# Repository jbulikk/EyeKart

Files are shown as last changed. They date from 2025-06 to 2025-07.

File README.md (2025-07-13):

# EyeKart

A gimbal system that mimics the user's head movements in real time.
The project is divided into two cooperating parts: a transmitting unit and a receiving unit.

- The transmitting module uses an IMU sensor to capture the user's head orientation.

- The motion data is processed and wirelessly transmitted to the receiving module.

- The receiving module interprets the incoming data and controls servo motors to adjust the mechanical gimbal accordingly, replicating the user's head movement.

imu_diagram
gimbal_diagram

# Overview

🎥 [Demo 1](https://youtu.be/xsn1YAiG0OE)  
🎥 [Demo 2](https://youtu.be/Qv6_rfJNsOU)

<br/>

IMG_E6707
IMG_E6706

<br/>

IMG_E6712

<br/>

IMG_E6708
IMG_E6710

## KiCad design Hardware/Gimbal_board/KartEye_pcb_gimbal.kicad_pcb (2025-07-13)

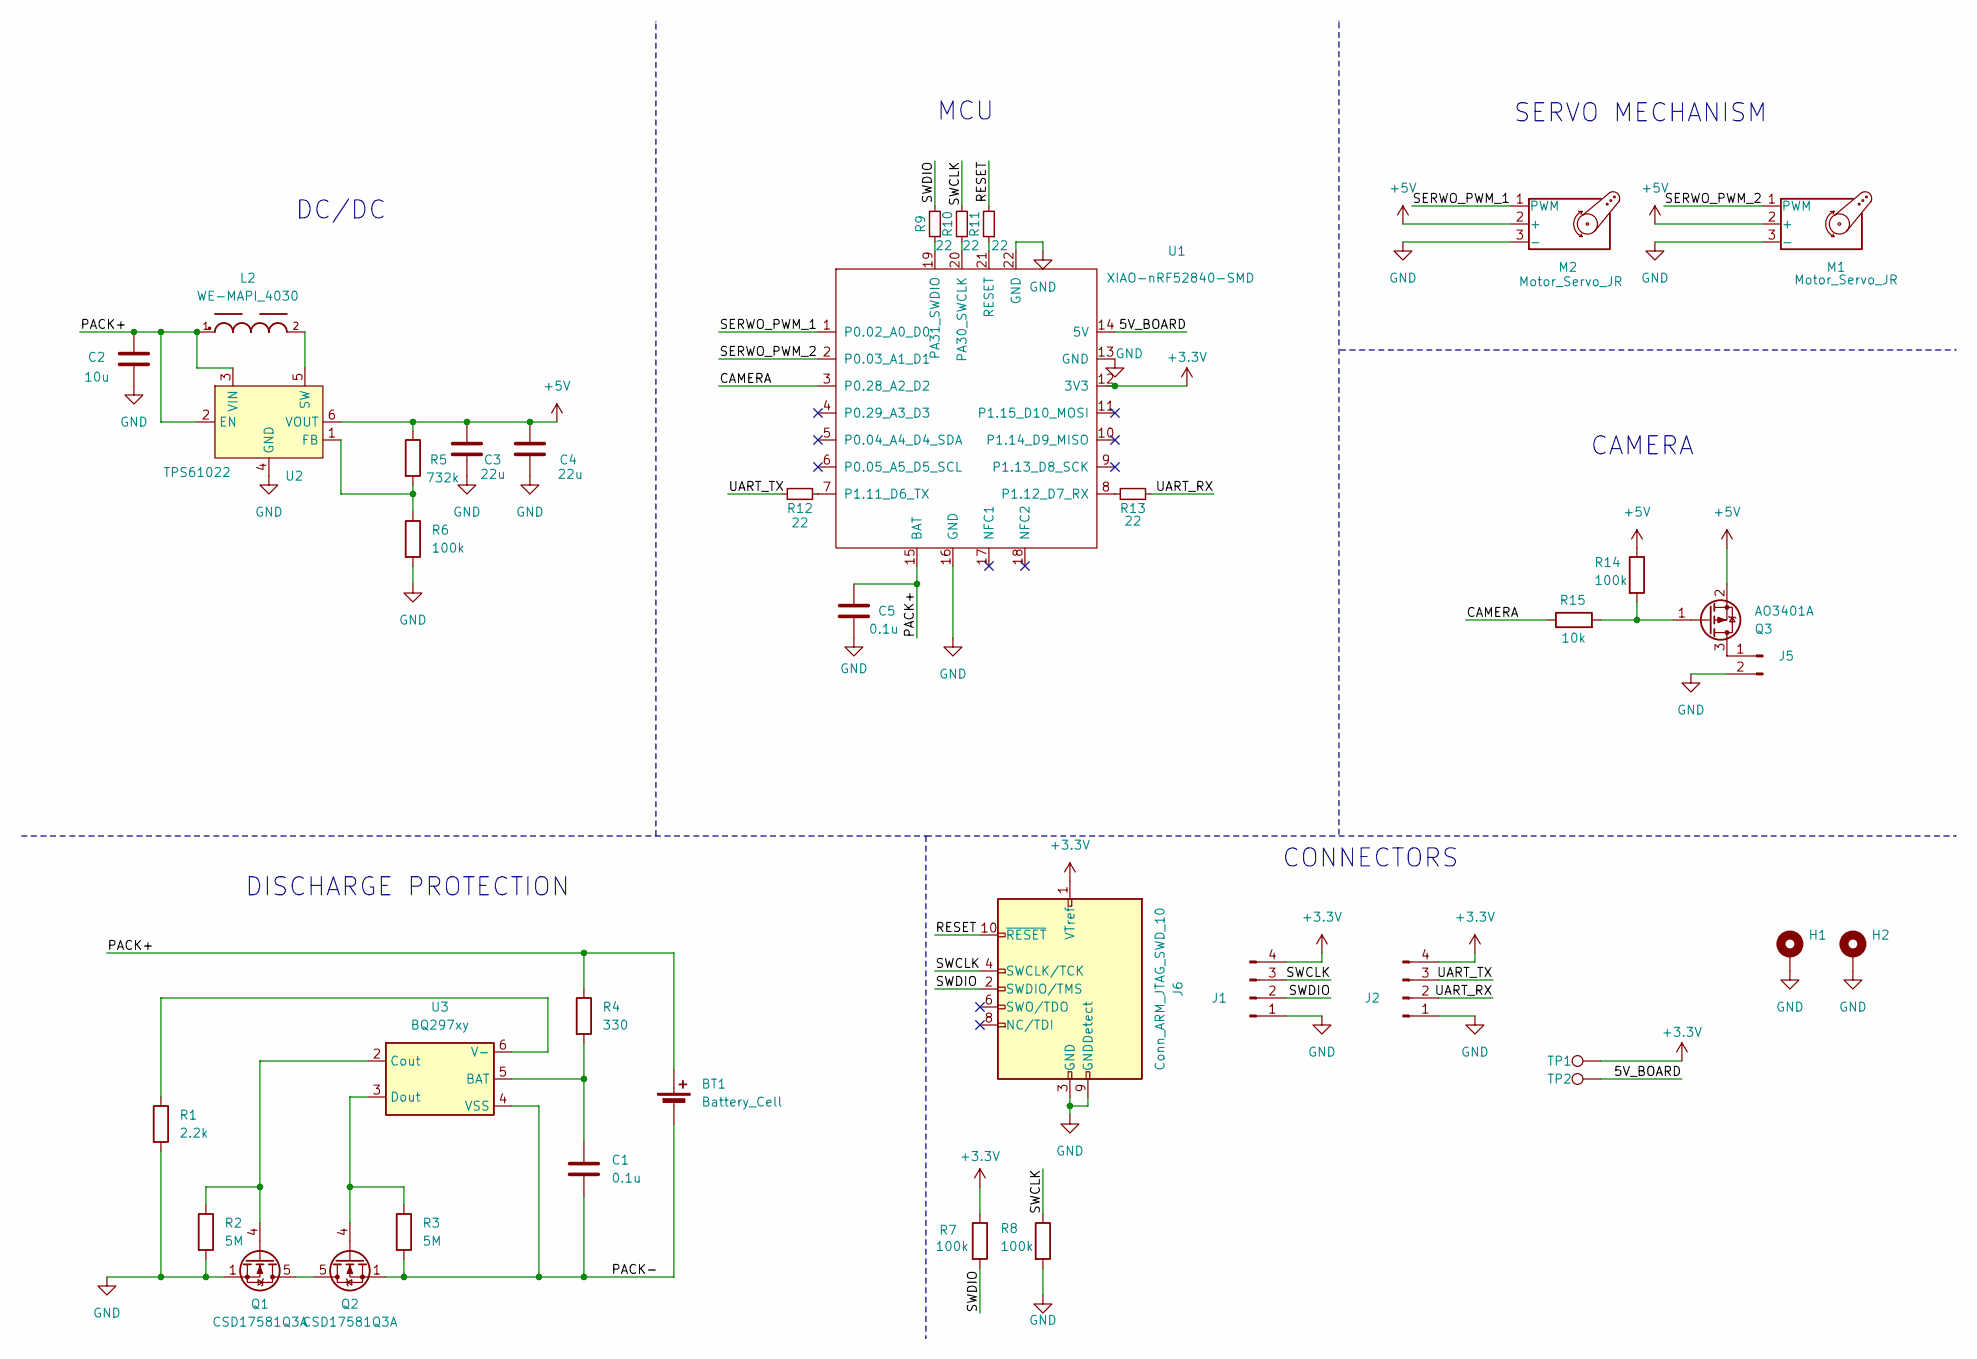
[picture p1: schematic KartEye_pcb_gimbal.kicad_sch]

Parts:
BT1: Battery_Cell; JST_XH_B2B-XH-A_1x02_P2.50mm_Vertical
C1, C5: 0.1u; C_0805_2012Metric_Pad1.18x1.45mm_HandSolder
C2: 10u; C_0805_2012Metric_Pad1.18x1.45mm_HandSolder
C3, C4: 22u; C_0805_2012Metric_Pad1.18x1.45mm_HandSolder
H1, H2: MountingHole_Pad; MountingHole_2.2mm_M2_DIN965_Pad
J1, J2: Conn_01x04_Pin; PinHeader_1x04_P2.54mm_Vertical
J5: Conn_01x02_Pin; Molex_PicoBlade_53047-0210_1x02_P1.25mm_Vertical
J6: Conn_ARM_JTAG_SWD_10; PinHeader_2x05_P1.27mm_Vertical_SMD
L2: WE-MAPI_4030
M1, M2: Motor_Servo_JR; PinHeader_1x03_P2.54mm_Vertical
Q1, Q2: CSD17581Q3A; VSON-8_3.3x3.3mm_P0.65mm_NexFET
Q3: AO3401A; SOT-23
R1: 2.2k; R_0805_2012Metric_Pad1.20x1.40mm_HandSolder
R2, R3: 5M; R_0805_2012Metric_Pad1.20x1.40mm_HandSolder
R4: 330; R_0805_2012Metric_Pad1.20x1.40mm_HandSolder
R5: 732k; R_0805_2012Metric_Pad1.20x1.40mm_HandSolder
R6, R7, R8, R14: 100k; R_0805_2012Metric_Pad1.20x1.40mm_HandSolder
R9, R10, R11, R12, R13: 22; R_0805_2012Metric_Pad1.20x1.40mm_HandSolder
R15: 10k; R_0805_2012Metric_Pad1.20x1.40mm_HandSolder
TP1, TP2: TestPoint; TestPoint_Pad_1.0x1.0mm
U1: XIAO-nRF52840-SMD
U2: TPS61022; SOT-563
U3: BQ297xy; WSON-6_1.5x1.5mm_P0.5mm

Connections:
+3.3V: J1.4, J2.4, J6.1 (VTref), R7.1, TP1.1, U1.12 (3V3)
+5V: C3.1, C4.1, M1.2 (+), M2.2 (+), Q3.2 (S), R5.1, R14.1, U2.6 (VOUT)
/5V_BOARD: TP2.1, U1.14 (5V)
/CAMERA: R15.1, U1.3 (P0.28_A2_D2)
/PACK+: BT1.1 (+), C2.1, C5.1, L2.1, R4.1, U1.15 (BAT), U2.2 (EN), U2.3 (VIN)
/PACK-: BT1.2 (-), C1.2, Q2.1 (S), Q2.2 (S), Q2.3 (S), R3.2, U3.4 (VSS)
/RESET: J6.10 (~RESET), R11.2
/SERWO_PWM_1: M2.1 (PWM), U1.1 (P0.02_A0_D0)
/SERWO_PWM_2: M1.1 (PWM), U1.2 (P0.03_A1_D1)
/SWCLK: J1.3, J6.4 (SWCLK/TCK), R8.1, R10.2
/SWDIO: J1.2, J6.2 (SWDIO/TMS), R7.2, R9.2
/UART_RX: J2.2, R13.1
/UART_TX: J2.3, R12.2
GND: C2.2, C3.2, C4.2, C5.2, H1.1, H2.1, J1.1, J2.1, J5.2, J6.3 (GND), J6.5 (GND), J6.9 (GNDDetect), M1.3 (-), M2.3 (-), Q1.1 (S), Q1.2 (S), Q1.3 (S), R1.2, R2.2, R6.2, R8.2, U1.13 (GND), U1.16 (GND), U1.22 (GND), U2.4 (GND)
unnamed: J5.1, Q3.3 (D)
unnamed: Q1.5 (D), Q2.5 (D)
unnamed: Q1.4 (G), R2.1, U3.2 (Cout)
unnamed: Q2.4 (G), R3.1, U3.3 (Dout)
unnamed: Q3.1 (G), R14.2, R15.2
unnamed: R12.1, U1.7 (P1.11_D6_TX)
unnamed: R13.2, U1.8 (P1.12_D7_RX)
unnamed: R10.1, U1.20 (PA30_SWCLK)
unnamed: R9.1, U1.19 (PA31_SWDIO)
unnamed: R11.1, U1.21 (RESET)
unnamed: R5.2, R6.1, U2.1 (FB)
unnamed: L2.2, U2.5 (SW)
unnamed: C1.1, R4.2, U3.5 (BAT)
unnamed: R1.1, U3.6 (V-)

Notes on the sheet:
CONNECTORS
SERVO MECHANISM
DC/DC
MCU
DISCHARGE PROTECTION
CAMERA

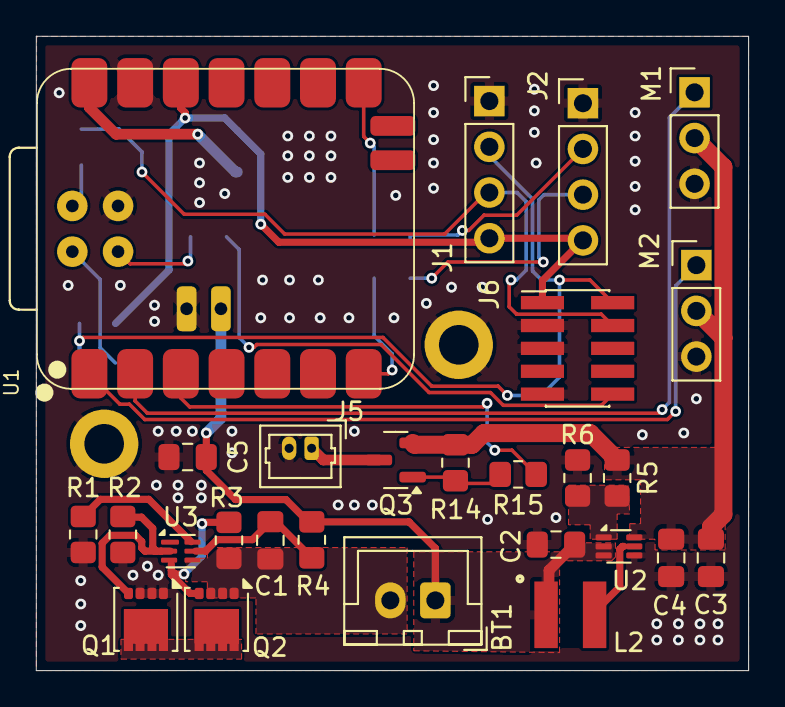
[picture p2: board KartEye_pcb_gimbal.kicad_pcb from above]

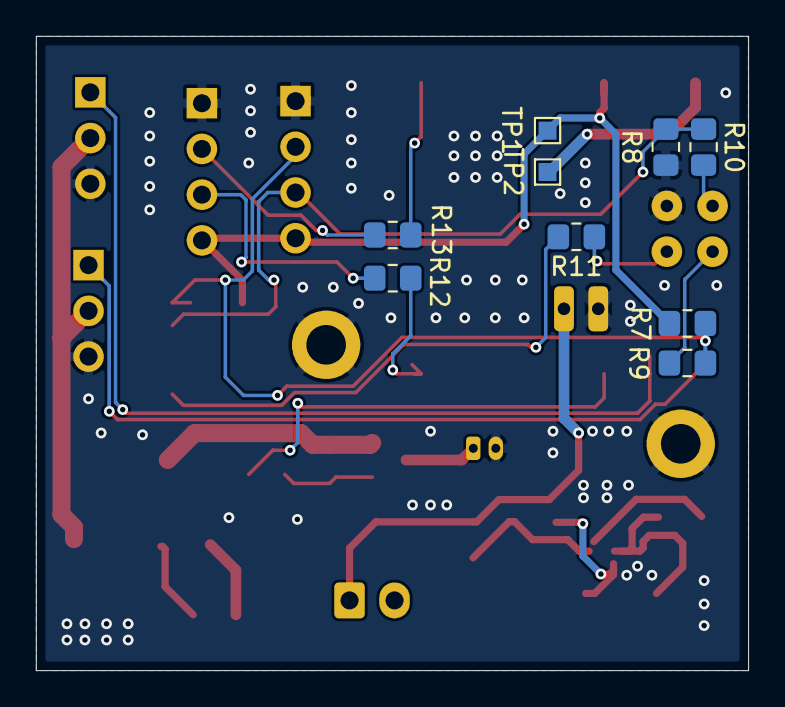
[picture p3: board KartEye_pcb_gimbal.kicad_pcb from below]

Board: 2 copper layers, 39.6 x 35.2 mm, 38 parts (9 on the bottom side), 28 nets.

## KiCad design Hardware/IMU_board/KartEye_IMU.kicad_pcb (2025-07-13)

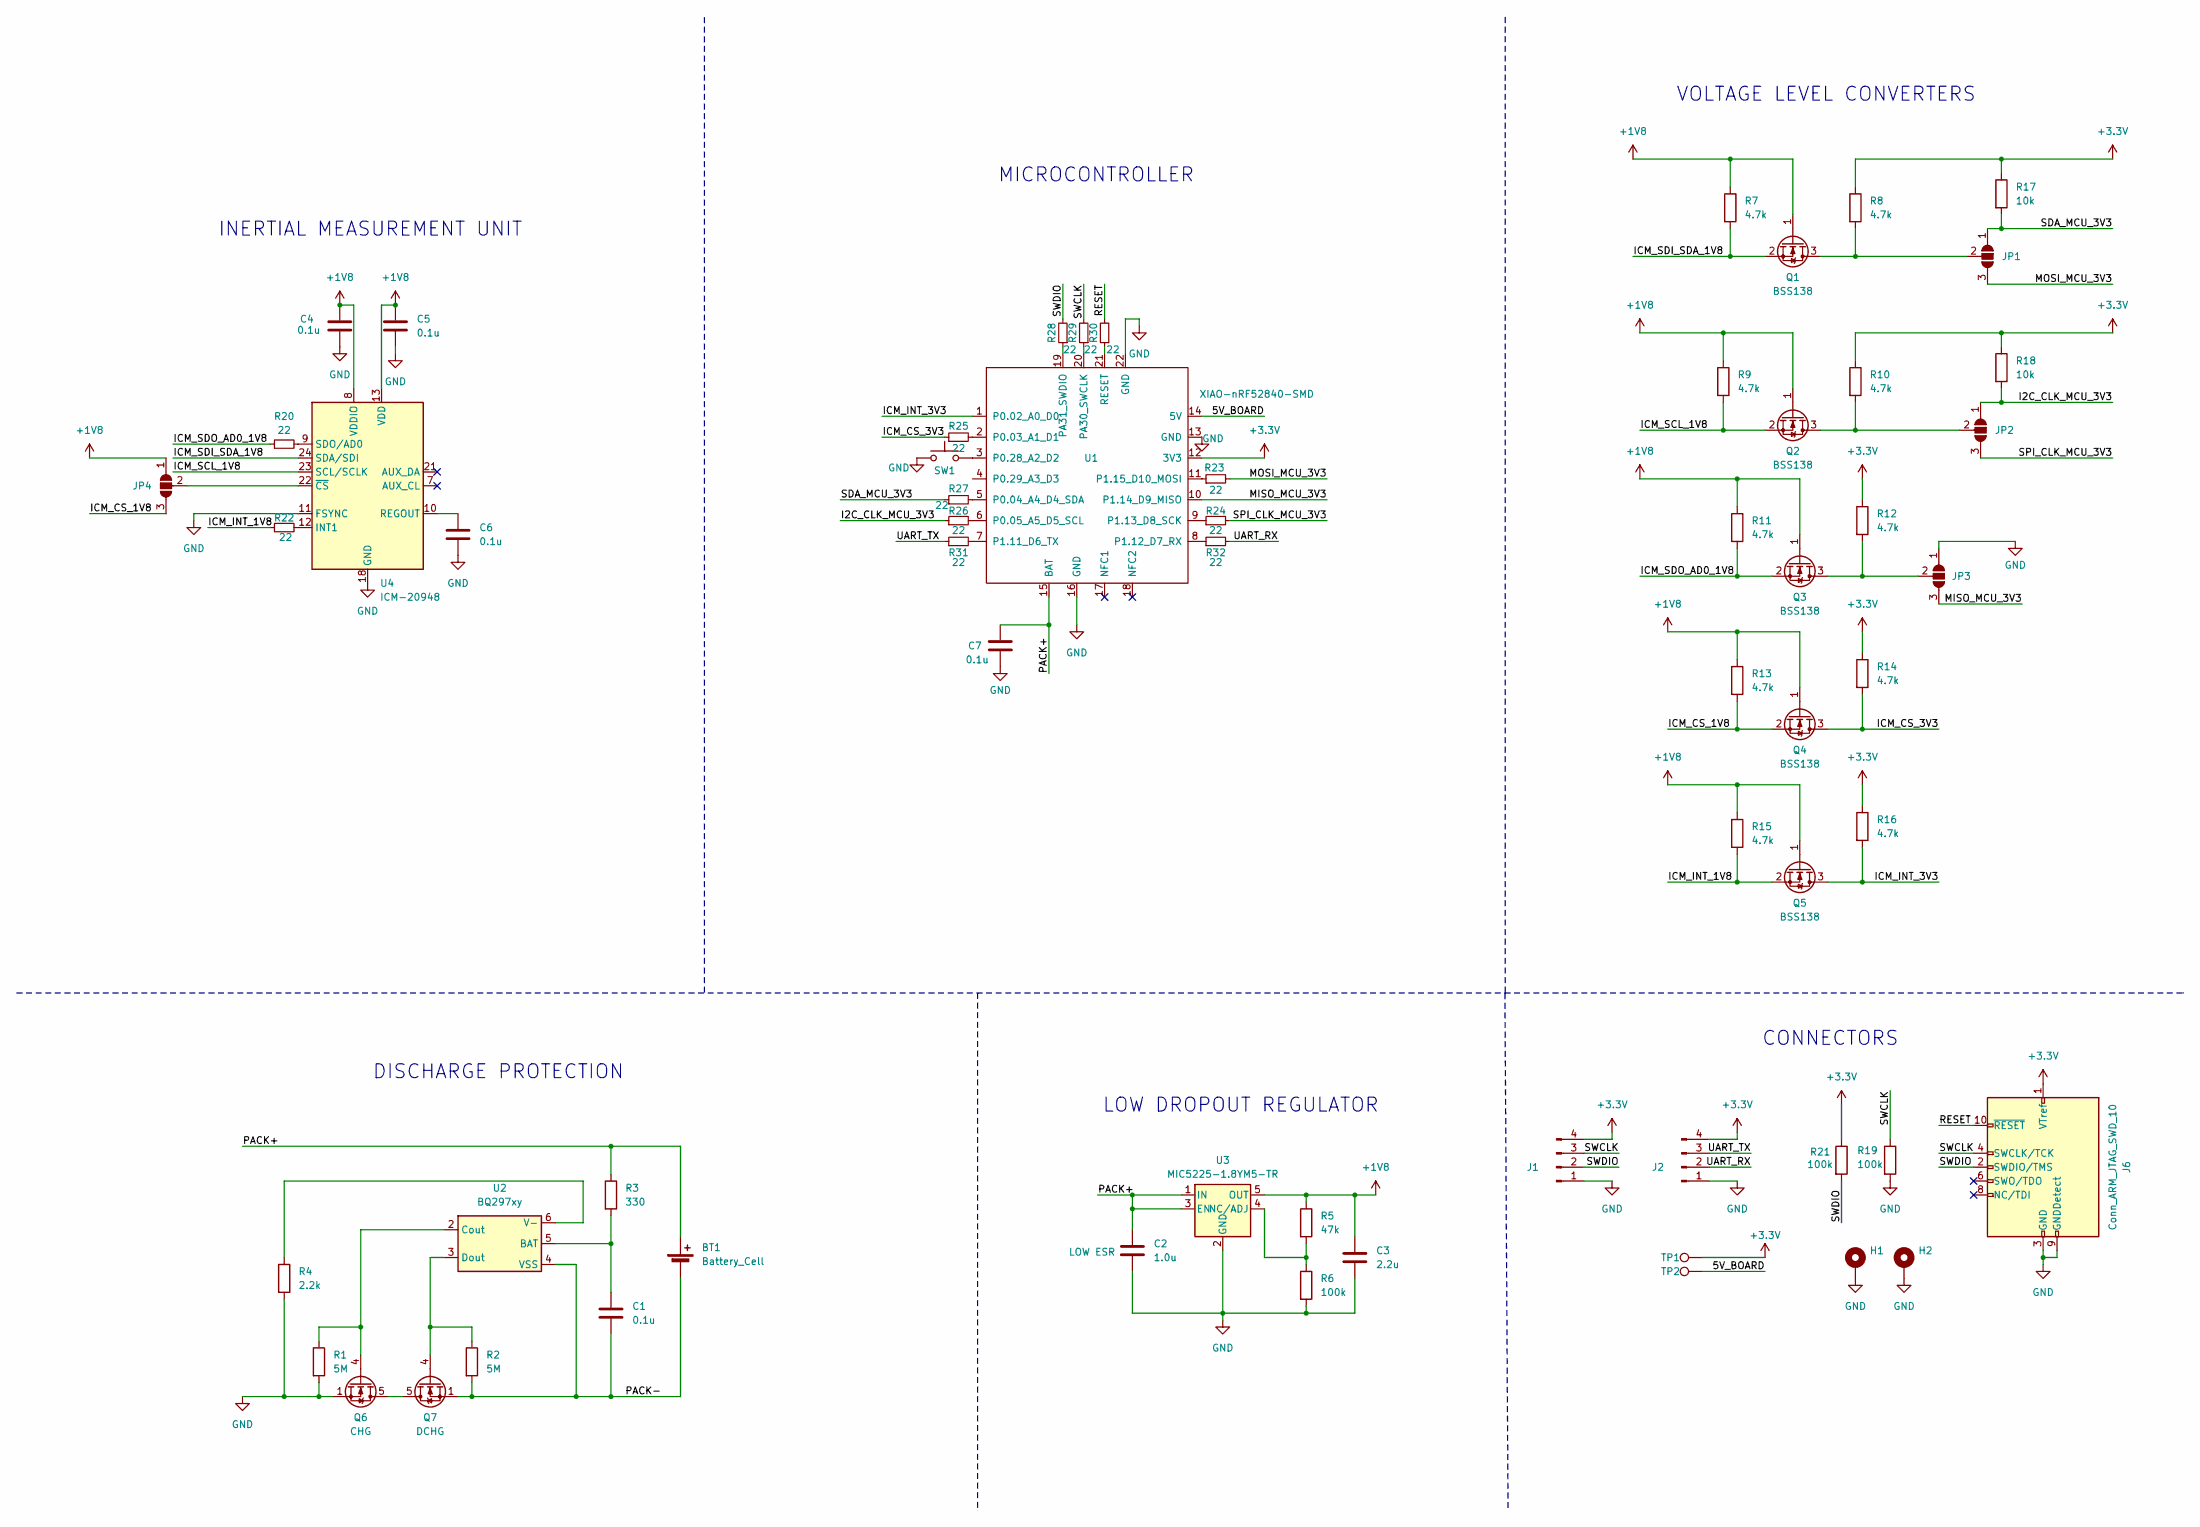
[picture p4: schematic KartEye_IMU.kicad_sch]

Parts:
BT1: Battery_Cell; JST_XH_B2B-XH-A_1x02_P2.50mm_Vertical
C1, C4, C5, C6, C7: 0.1u; C_0805_2012Metric_Pad1.18x1.45mm_HandSolder
C2: 1.0u; C_0805_2012Metric_Pad1.18x1.45mm_HandSolder
C3: 2.2u; C_0805_2012Metric_Pad1.18x1.45mm_HandSolder
H1, H2: MountingHole_Pad; MountingHole_2.2mm_M2_DIN965_Pad
J1, J2: Conn_01x04_Pin; PinHeader_1x04_P2.54mm_Vertical
J6: Conn_ARM_JTAG_SWD_10; PinHeader_2x05_P1.27mm_Vertical_SMD
JP1, JP2, JP3, JP4: SolderJumper_3_Open; SolderJumper-3_P1.3mm_Open_RoundedPad1.0x1.5mm_NumberLabels
Q1, Q2, Q3, Q4, Q5: BSS138; SOT-23_Handsoldering
Q6: CHG; VSON-8_3.3x3.3mm_P0.65mm_NexFET
Q7: DCHG; VSON-8_3.3x3.3mm_P0.65mm_NexFET
R1, R2: 5M; R_0805_2012Metric_Pad1.20x1.40mm_HandSolder
R3: 330; R_0805_2012Metric_Pad1.20x1.40mm_HandSolder
R4: 2.2k; R_0805_2012Metric_Pad1.20x1.40mm_HandSolder
R5: 47k; R_0805_2012Metric_Pad1.20x1.40mm_HandSolder
R6, R19, R21: 100k; R_0805_2012Metric_Pad1.20x1.40mm_HandSolder
R7, R8, R9, R10, R11, R12, R13, R14, R15, R16: 4.7k; R_0805_2012Metric_Pad1.20x1.40mm_HandSolder
R17, R18: 10k; R_0805_2012Metric_Pad1.20x1.40mm_HandSolder
R20, R22, R23, R24, R25, R26, R27, R28, R29, R30, R31, R32: 22; R_0805_2012Metric_Pad1.20x1.40mm_HandSolder
SW1: SW_Push; SW_SPST_CK_RS282G05A3
TP1, TP2: TestPoint; TestPoint_Pad_1.0x1.0mm
U1: XIAO-nRF52840-SMD
U2: BQ297xy; WSON-6_1.5x1.5mm_P0.5mm
U3: MIC5225-1.8YM5-TR; SOT-23-5
U4: ICM-20948; InvenSense_QFN-24_3x3mm_P0.4mm

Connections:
+1V8: C3.1, C4.1, C5.1, JP4.1 (A), Q1.1 (G), Q2.1 (G), Q3.1 (G), Q4.1 (G), Q5.1 (G), R5.1, R7.1, R9.1, R11.1, R13.1, R15.1, U3.5 (OUT), U4.8 (VDDIO), U4.13 (VDD)
+3.3V: J1.4, J2.4, J6.1 (VTref), R8.1, R10.1, R12.1, R14.1, R16.1, R17.1, R18.1, R21.1, TP1.1, U1.12 (3V3)
/5V_BOARD: TP2.1, U1.14 (5V)
/I2C_CLK_MCU_3V3: JP2.1 (A), R18.2, R26.1
/ICM_CS_1V8: JP4.3 (B), Q4.2 (S), R13.2
/ICM_CS_3V3: Q4.3 (D), R14.2, R25.1
/ICM_INT_1V8: Q5.2 (S), R15.2, R22.1
/ICM_INT_3V3: Q5.3 (D), R16.2, U1.1 (P0.02_A0_D0)
/ICM_SCL_1V8: Q2.2 (S), R9.2, U4.23 (SCL/SCLK)
/ICM_SDI_SDA_1V8: Q1.2 (S), R7.2, U4.24 (SDA/SDI)
/ICM_SDO_AD0_1V8: Q3.2 (S), R11.2, R20.1
/MISO_MCU_3V3: JP3.3 (B), U1.10 (P1.14_D9_MISO)
/MOSI_MCU_3V3: JP1.3 (B), R23.2
/PACK+: BT1.1 (+), C2.1, C7.1, R3.1, U1.15 (BAT), U3.1 (IN), U3.3 (EN)
/PACK-: BT1.2 (-), C1.2, Q7.1 (S), Q7.2 (S), Q7.3 (S), R2.2, U2.4 (VSS)
/RESET: J6.10 (~RESET), R30.2
/SDA_MCU_3V3: JP1.1 (A), R17.2, R27.1
/SPI_CLK_MCU_3V3: JP2.3 (B), R24.2
/SWCLK: J1.3, J6.4 (SWCLK/TCK), R19.1, R29.2
/SWDIO: J1.2, J6.2 (SWDIO/TMS), R21.2, R28.2
/UART_RX: J2.2, R32.2
/UART_TX: J2.3, R31.1
GND: C2.2, C3.2, C4.2, C5.2, C6.2, C7.2, H1.1, H2.1, J1.1, J2.1, J6.3 (GND), J6.5 (GND), J6.9 (GNDDetect), JP3.1 (A), Q6.1 (S), Q6.2 (S), Q6.3 (S), R1.2, R4.2, R6.2, R19.2, SW1.1, U1.13 (GND), U1.16 (GND), U1.22 (GND), U3.2 (GND), U4.11 (FSYNC), U4.18 (GND), U4.20 (GND)
unnamed: JP1.2 (C), Q1.3 (D), R8.2
unnamed: JP2.2 (C), Q2.3 (D), R10.2
unnamed: JP3.2 (C), Q3.3 (D), R12.2
unnamed: JP4.2 (C), U4.22 (~CS)
unnamed: Q6.5 (D), Q7.5 (D)
unnamed: Q6.4 (G), R1.1, U2.2 (Cout)
unnamed: Q7.4 (G), R2.1, U2.3 (Dout)
unnamed: R25.2, U1.2 (P0.03_A1_D1)
unnamed: R27.2, U1.5 (P0.04_A4_D4_SDA)
unnamed: R26.2, U1.6 (P0.05_A5_D5_SCL)
unnamed: SW1.2, U1.3 (P0.28_A2_D2)
unnamed: R31.2, U1.7 (P1.11_D6_TX)
unnamed: R32.1, U1.8 (P1.12_D7_RX)
unnamed: R24.1, U1.9 (P1.13_D8_SCK)
unnamed: R23.1, U1.11 (P1.15_D10_MOSI)
unnamed: R29.1, U1.20 (PA30_SWCLK)
unnamed: R28.1, U1.19 (PA31_SWDIO)
unnamed: R30.1, U1.21 (RESET)
unnamed: C1.1, R3.2, U2.5 (BAT)
unnamed: R4.1, U2.6 (V-)
unnamed: R5.2, R6.1, U3.4 (NC/ADJ)
unnamed: R22.2, U4.12 (INT1)
unnamed: C6.1, U4.10 (REGOUT)
unnamed: R20.2, U4.9 (SDO/AD0)

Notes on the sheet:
INERTIAL MEASUREMENT UNIT
LOW DROPOUT REGULATOR
DISCHARGE PROTECTION
VOLTAGE LEVEL CONVERTERS
CONNECTORS
MICROCONTROLLER

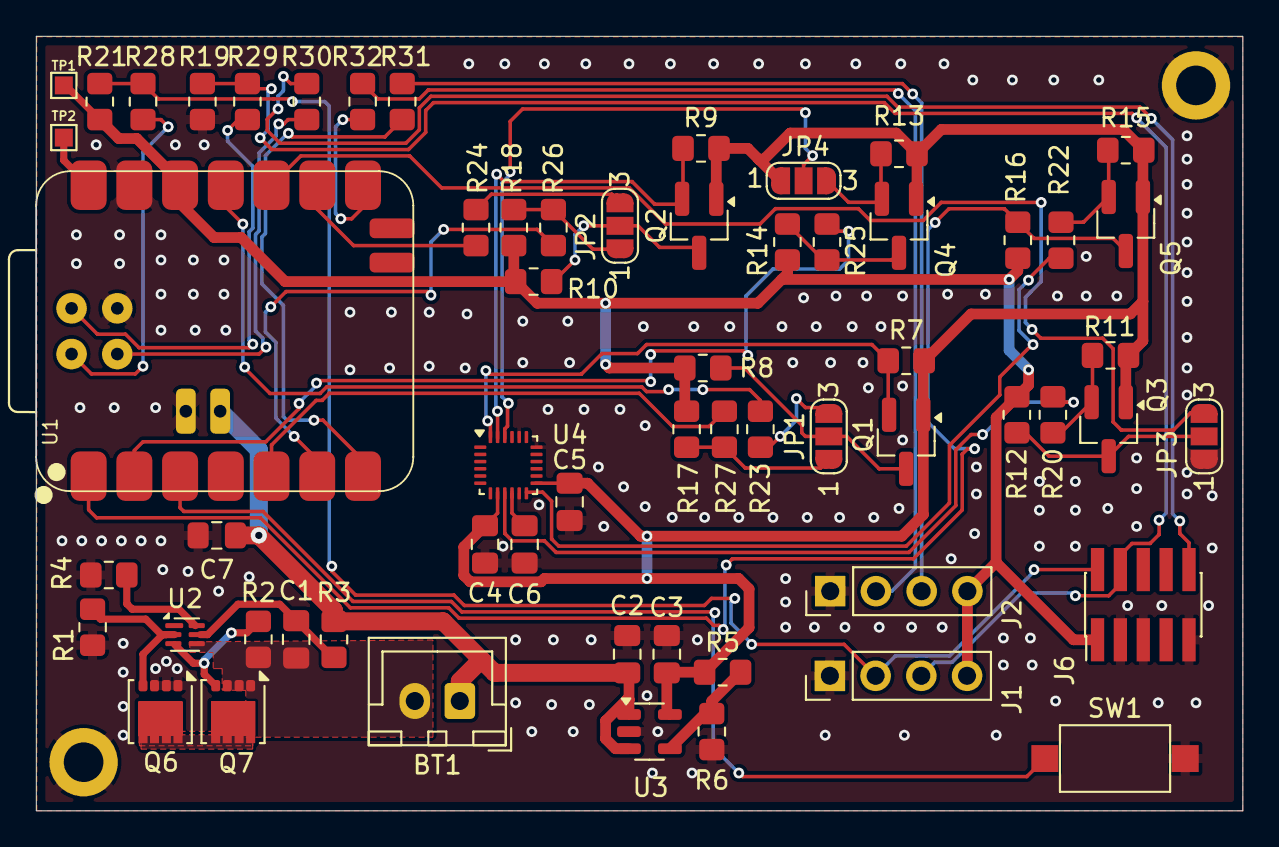
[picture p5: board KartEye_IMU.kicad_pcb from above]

Board: 2 copper layers, 67.0 x 43.0 mm, 63 parts (0 on the bottom side), 47 nets.

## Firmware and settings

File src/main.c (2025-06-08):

#include <zephyr/kernel.h>
#include <zephyr/sys/printk.h>
#include <zephyr/device.h>
#include "ICM20948.h"

#define I2C_DEV_LABEL "I2C_0"

ImuData imu;


// BT PERIPHERAL
static void on_receive(const char *data) {
    // float data_f = (float)*data;
    // printk("Peripheral received: %f\n", data_f);
    printk("Peripheral received: %s\n", data);
}

static void led_timer_callback(struct k_timer *timer_id)
{
	led_toggle();
	// bt_central_send("Hello from timer");
}
K_TIMER_DEFINE(led_timer, led_timer_callback, NULL);

// BT CENTRAL
static void on_connected(void) {
    printk("Connected to peripheral.\n");
}


static void send_angle_callback(struct k_timer *timer_id)
{
    char message[16];
    snprintf(message, sizeof(message), "%.2f, %.2f", imu.pitch_complementary, imu.roll_complementary); 
    
    printk("Sending %s\n", message);
    bt_central_send(message);  // Send the whole string, not a single char
}
K_TIMER_DEFINE(send_angle_timer, send_angle_callback, NULL);


int main(void) {
    led_init();
	k_timer_start(&led_timer, K_SECONDS(1), K_SECONDS(1));

    printk("Start of main\n");
    bt_central_init(on_connected);
	k_timer_start(&send_angle_timer, K_MSEC(300), K_MSEC(300));

    const struct device *i2c_dev = device_get_binding(I2C_DEV_LABEL);
    if (!i2c_dev) {
        printk("I2C device not found: %s\n", I2C_DEV_LABEL);
        return 0;
    }

    icm_read_whoami(i2c_dev);
    

    printk("Initializing ICM-20948...\n");
    icm_init(i2c_dev);

    printf("Start loop...\n");

    while (1) {
        icm_read_acc_mag_temp(i2c_dev, &imu);

        k_sleep(K_MSEC(1));
    }
}

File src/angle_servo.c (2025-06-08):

#include "angle_servo.h"

int angle_servo_init(angle_servo_t *as, const servo_dt_spec *servo, float min_angle, float max_angle)
{
    if (!servo_is_ready_dt(servo))
        return 0;

    as->servo = *servo;
    as->min_angle = min_angle;
    as->max_angle = max_angle;
    float range_angle = max_angle - min_angle;
    float range_pulse = (float)(servo->max_pulse - servo->min_pulse);
    if (0.0f == range_angle)
        as->ratio = 0.0f;
    else
        as->ratio = (range_pulse / range_angle);
    return 1;
}

int angle_servo_set_angle(const angle_servo_t *as, float angle_deg)
{
    if (angle_deg < as->min_angle)
        angle_deg = as->min_angle;
    if (angle_deg > as->max_angle)
        angle_deg = as->max_angle;
    uint32_t pulse = as->servo.min_pulse + (uint32_t)((angle_deg - as->min_angle) * as->ratio);
    return servo_set_pulse(&as->servo, pulse);
}

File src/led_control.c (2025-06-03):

#include "led_control.h"
#include <zephyr/sys/printk.h>

static const struct gpio_dt_spec led = GPIO_DT_SPEC_GET(LED0_NODE, gpios);
static bool led_initialized = false;

int led_init(void)
{
    if (!gpio_is_ready_dt(&led)) {
        printk("LED device not ready\n");
        return -ENODEV;
    }

    int ret = gpio_pin_configure_dt(&led, GPIO_OUTPUT_ACTIVE);
    if (ret < 0) {
        printk("Failed to configure LED pin\n");
        return ret;
    }

    led_initialized = true;
    return 0;
}

int led_toggle(void)
{
    if (!led_initialized) {
        printk("LED not initialized\n");
        return -EIO;
    }

    return gpio_pin_toggle_dt(&led);
}

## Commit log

2025-06-03 initial code
    [pwm-servo.yaml]
2025-06-06 reading who_am_i and scanning i2c
2025-06-07 add servo files
2025-06-07 working calculating pitch and yaw, enabled printing float values
2025-06-07 Imu with BT protocol
2025-06-08 adjusting complementary filter
2025-06-08 update gitignore, fix errors
    [angle_servo.c, main.c]
2025-07-13 Adding hardware files
    [KartEye_IMU.kicad_pcb, KartEye_IMU.kicad_sch, KartEye_pcb_gimbal.kicad_pcb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]
